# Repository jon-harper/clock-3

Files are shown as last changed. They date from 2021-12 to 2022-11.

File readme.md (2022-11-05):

# Clock 3

| First Print | Completed Panels |
|---|---|
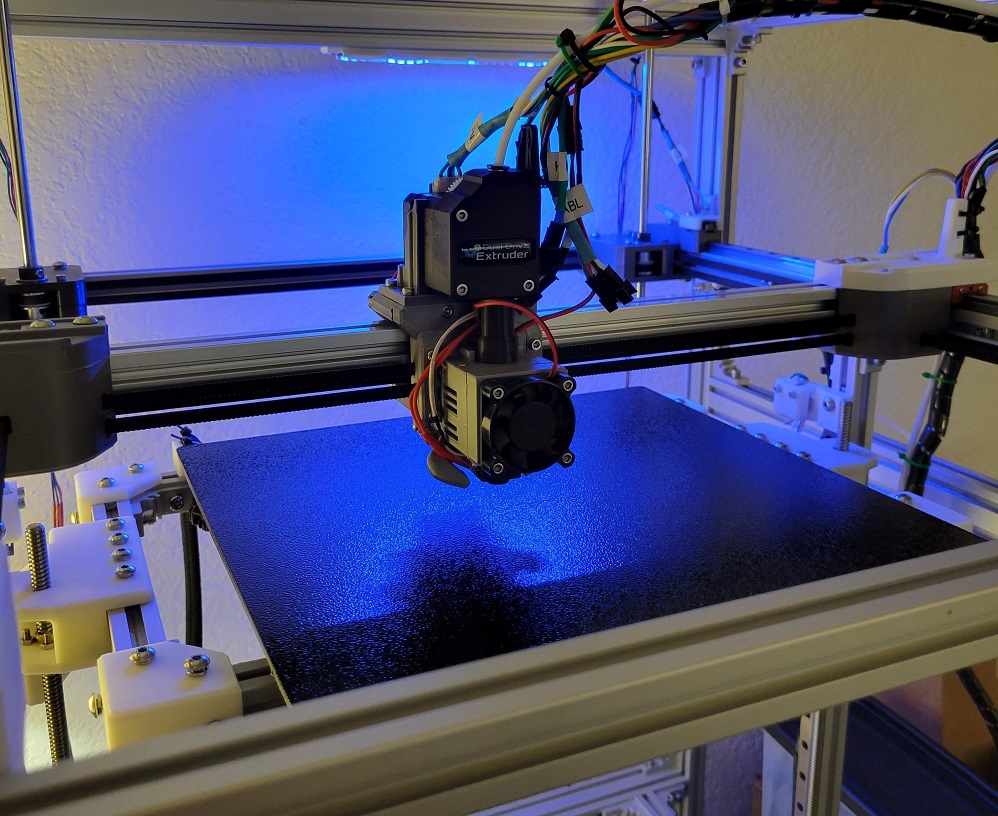
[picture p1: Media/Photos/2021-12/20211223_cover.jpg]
Cover photo of hotend
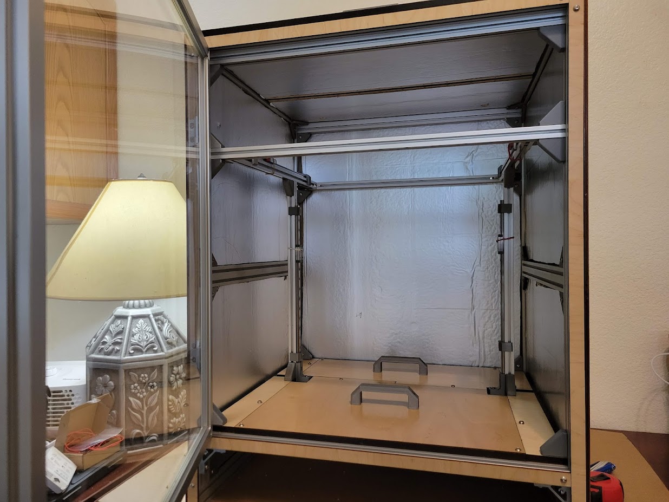
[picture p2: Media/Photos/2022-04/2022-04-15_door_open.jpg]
Cover photo with door open
|  |  |

This is the evolution of the concept of a fully enclosed, temperature-controlled 3D printer with externally mounted steppers motors. The idea of building an enclosed 3D printer to suit my specific needs came during the 2021 Winter Storm. Clock 1 was a thought experiment to enclose an Ender 5-like Cartesian printer. Clock 2 was a from-scratch CoreXY printer that I largely built before acquiring the ability to safely print ABS.

Clock 3 is a complete redesign incorporating most of the common, off-the-shelf components from Clock 2. It incorporates lessons from repeated assembly/disassembly of Clock 2, successful concepts from other projects, and a lot of experimentation with ABS in an enclosure. Clock 3 is a working name for this project and is not final.

## Status

The core Fusion 360 files are pretty trashed due to interdependancies. I've had to halt development for now.

~~Documentation of the initial prootype is ongoing and active. The most recent compiled markdown can be viewed at [jon-harper.github.io/clock-3/](https://jon-harper.github.io/clock-3/). Follow-on releases will address minor issues discovered in the process that do not require immediate resolution.~~

## Notes

- Klipper firmware for Clock 3 is available [here](../clock3-klipper).
- The Clock Face project is [here](../clock-face), which revises the physical display and menu system for Klipper.
- The Fusion 360 model is not published yet, but you can find the project's Python scripts [here](../Clock3Scripts)
- This project is very much under active development, [**first printing on 12/21/2021**](/Media/Cropped/20211221_Hotend.jpg).
- Head to the [Media](/Media) folder for renders and photos of the prototype.

# Organization

## Naming Scheme

### STL Files

STLs are numbered sequentially to help with assembly. The number of each component is printed discreetly on each piece so that it is either concealed or very hard to see after installation. Each *component* falls into one of several *categories* and is identified by either its name or location. Components that come in left and right versions have *chirality*.

The printed text on each component also include an L or R for chiral components to help with identification. Some miscellanious and very basic parts lack numbers due to size or geometry constraints.

Example: `01 - XY - Pulleys - L Bottom.stl`

You can find all of the printable files in the [STL](STL/) folder along with a list of [part codes](Docs/Part%20Codes.md).

### Component Labeling

What one board labels as "THB" another may label as "TB". Likewise, endstop/limit switch connector abbreviations (and pin order!) are not standard, inasmuch as anything in 3D printing is standardized. To that end, a single nomenclature is adopted for part labels. Each connector has a two- or three-letter code for labeling panels and wiring. Your actual wiring may use a different system, but printed parts with labels follow this pattern. It is recommended for continuity with printed parts and documentation to use the same. The full part list may be found in the [`Docs`](Docs/) folder.

## Misc.

There are a number of tools to help determine parametric details such as the ideal M5 screw hole size or the proper hole size for your brand of brass inserts. These can be found in the `STL/Tools` folder and are meant to be printed. The results can be fed back in to the Fusion model and then exported for printing. Stock exported STL files will come with default tolerances and may not fit as precisely.

There is also a `CAD/Tools` folder with parametric tools such as an LED channel.

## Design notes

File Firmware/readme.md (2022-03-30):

# Firmware for Clock 3

Clock 3 runs on Klipper. Marlin and/or RepRapFirmware *might* be able to run the printer, but a lot of features would be missing, such as the camera.

## Klipper Config Files

You can find the `.cfg` files in the [clock3-klipper](../../../../clock3-klipper) repository. It's a separate repository so that it can be cloned directly into a subdirectory of your `~/klipper_config` directory.

## Macros?

As I build up a collection of Klipper macros, I will create an additional repository for general Klipper macros. Any Clock 3-specific macros will likely be part of the [clock3-klipper](../../../../clock3-klipper) repository.

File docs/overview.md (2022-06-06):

---
title: Overview
summary: General overview page for the documentation.
authors: Jon Harper
date: 2022-04-09
---

This site acts as a central documentation point for the Clock 3 project.

## About

For an overview, see the About section pages:

- A list of [features](about/features.md)
- A [gallery](about/gallery.md) of renders and prototype photos
- [Development goals](about/goals.md) for this project
- [Frequently Asked Questions](about/faq.md)

## Status

The Status section contains more details:

- A regularly updated [changelog](status/changelog.md)
- The current and past [releases](status/releases.md)
- The release [roadmap](status/roadmap.md)

## Documentation

In addition, there are help and guides for:

- Sourcing materials
- Fabricating parts
- Assembly (*in progress*)
- Initial configuration (*pending*)

This is a large project with one developer, so this documentation will evolve iteratively and gradually. Feedback is welcome via the [GitHub repository](https://github.com/jon-harper/clock3-docs).

### Bill of Materials

This documentation includes a general [Sales Bill of Materials](/bom/) to guide purchasing and decision making. This is a list of what you will need to actually purchase or have on hand. Some of the materials will need to be modified, fabricated, or permanently used to make other parts before or during assembly. The list of all parts once the raw materials are consumed and ready for assembly is the [Assembly Bill of Materials]().

Think of the Sales BOM as what you need to buy; the Assembly BOM is what you'll use to build.

The Clock 3 repository contains a [more detailed version of these files](https://github.com/jon-harper/clock-3/tree/main/BOM).

### Assembly

We've assembled and then broken down the Clock 3 prototype repeatedly so that you don't have to do the same with yours. Assembly of Clock 3 is meant to be logical, intuitive, and easy: every wire is pre-measured, every heated insert accounted for.

It's a time investment to get everything ready, but the result is a very straightforward assembly process.

### Configuration

Clock 3 runs on [MainsailOS](https://github.com/mainsail-crew/MainsailOS), which is an all-in-one OS for running [Klipper](https://www.klipper3d.org/) firmware with a clean web frontend.

Clock 3 relies on a modified Klipper 12864 menu system and display with more functionality than the stock menu system. 

We've setup several repositories so that you can simply `git clone` the configuration files directly onto your Raspberry Pi in the appropriate directories.

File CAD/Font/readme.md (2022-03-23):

# Hack, a Font Face

This project uses [Hack](https://sourcefoundry.org/hack/#download) as a general-purpose, easily printable, monospace font. You'll need to download it to open the source model in Fusion 360.

There's a [download page](https://sourcefoundry.org/hack/#download) or you can grab them from this Git source folder.

It's also a great font face for coding or scripting if you need a new one.

Hack is released under the [MIT license](https://github.com/source-foundry/Hack/blob/master/LICENSE.md). A copy is in this folder, as well.

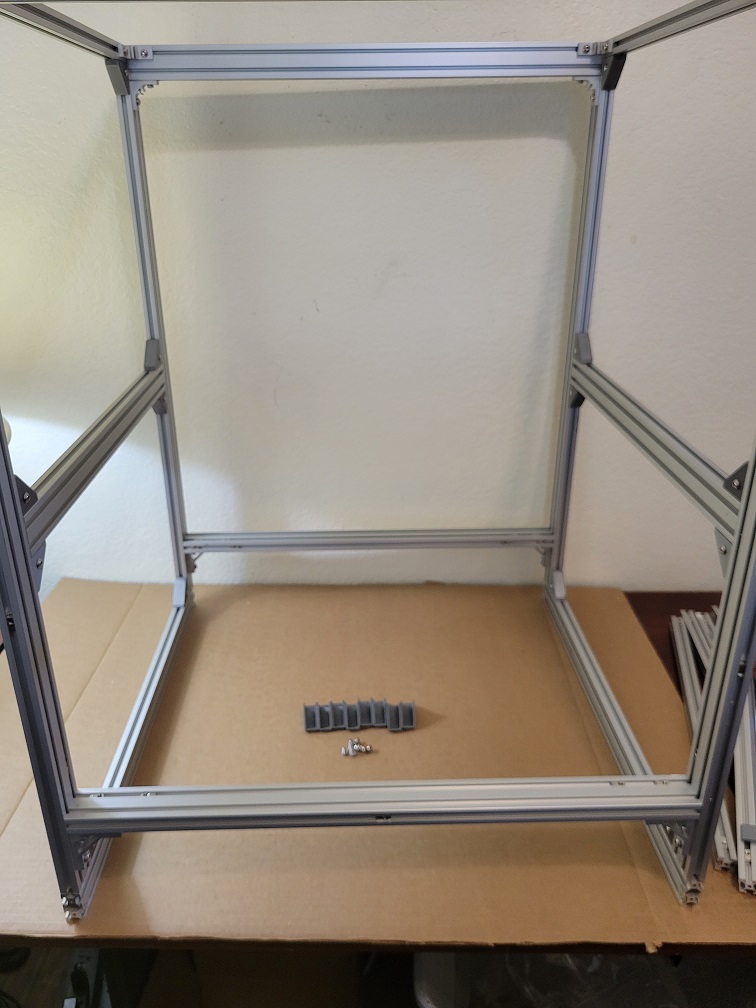
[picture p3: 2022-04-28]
docs/img/bracket_covers_center/brackets_overview.jpg

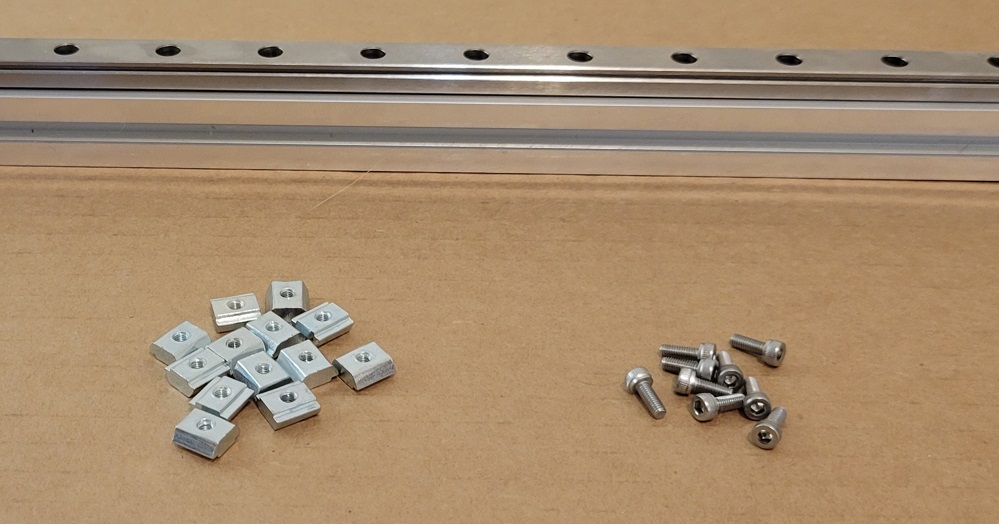
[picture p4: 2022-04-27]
docs/img/rail_install/overview.jpg

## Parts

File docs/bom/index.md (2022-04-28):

---
title: Bill of Materials Introduction
summary: An introduction to reading the Clock 3 Bill of Materials.
authors: Jon Harper
date: 2022-04-05
---

*This document is actively being refined and edited for mistaeks.*
## Overview

We designed Clock 3 with several rules related to sourcing and parts in mind:

- Every new line added to the BOM has an up front cost.
- Rare parts are expensive and hard to find, by definition.
- Standardized and *de facto* standard parts are cheaper and have more suppliers.
- Custom fabricated anything is expensive.

With those rules in mind, we aim to both keep costs down and make sourcing parts as simple as possible.

## Keeping Track

Every component that goes in to making a Clock 3 printer is assigned an ID number and categorized in several ways.
 
- Is it a printed part or something purchased?
- Does it require modification or assembly, such as finished cables or insulation cut to size?
- Is it an aid for assembly or maintence that isn't part of the printer itself?
- Finally, what is the general function of the part in the printer (e.g. frame, electronics, motion)?

## Categorization

Let's talk about identifying the things you'll need to print, buy, or make. Parts are given a number with a two letter prefix and a three-digit number code, for example `PN001`.

### Prefixes

`MN`: Parts in the format `MN###` are raw materials. During the assembly process, they'll be modified or used to make something else. Typically this can't be reversed: examples are connector pins and heat shrink tubing. This list is not exhaustive--if you won't need to buy or assemble it, it's not given a number. For example, you probably won't cut the frame extrusions yourself, so we don't include the raw aluminum in the list.

`UN`: These parts aren't actually part of the printer but you will need them to put it together or keep it running. You may already have some or all of these on hand, like a soldering iron or set of Metric hex wrenches.

`PN`: These are finished parts, whether printed, purchased, or made from materials. They come in the format `PN###`.

!!! note
    If the number after `PN` is less than 399, it's a printed part.

### Fabricated parts

There are several kinds of these:

- Printed parts, with or without heat set inserts
- Cables and wiring harnesses
- Cut extrusions and panels

With the exception of cables, all of these have part numbers in the form `PN`. Cables also have an ID, but it is tracked based on the component that the cable powers. There's more on that later in the assembly guide.

All of these fabricated parts require materials (parts starting with `MN`). Consequently, some parts in the BOM are made entirely from materials.

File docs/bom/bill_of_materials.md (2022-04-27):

# Bill of Materials

The columns of this list are abbreviated for readability and reference. The
[Excel spreadsheet](https://github.com/jon-harper/clock-3/blob/main/BOM/bill_of_materials.xlsx)
version contains additional columns that are helpful in sourcing.

!!! warning
    The script that auto-generates this list does not read decimal values. Anything measured in length
    is measured in centimeters (cm) instead of meters (m) to work around this.
    
!!! note
    - Materials are used in fabricating parts found later in the Bill of Materials or cable
      list. Some parts, particularly the acrylic and wood panels, will likely require outside
      fabrication.
    - All reference URLs and suppliers are purely for assistance in sourcing materials and are
      not endorsed.
    - The "Supplies" category includes a large number of components that are often already in the
      hands of experienced makers. As such, the list is primarily for reference and is not formally
      part of the Bill of Materials.

## Materials

| ID | Description | UOM | Qty | Notes |
|:---|:---|----:|----:|:---|
| MN001 | [Activated Carbon, Virgin Coconut, 4-8mm](https://www.amazon.com/gp/product/B00XIIH43W) | 1 | lb | 0.5lb to start; have heard negative things about this supplier recently |
| MN002 | [Thermal Glue](https://www.amazon.com/gp/product/B07TSH6MNT) | 1 | ea |  |
| MN004 | [Zip ties, 4"](https://www.amazon.com/AmazonBasics-Multi-Purpose-Cable-Ties-200-Piece/dp/B087MKMSDY) | 1 | pk | Qty varies based on cofiguration and personal preference |
| MN100 | [Polyisocyanurate Foam, 1/2", 4'x8' sheet](https://www.homedepot.com/p/RMAX-Pro-Select-R-Matte-Plus-3-1-2-in-x-4-ft-x-8-ft-R-3-2-Foam-Insulation-Board-637902/313501506) | 1 | ea | Can substitute 3/4" and 1" in places for better insulation |
| MN101 | Plywood sheet, 12mm thickness, 4'x5' | 2 | ea | For paneling |
| MN102 | Acrylic sheet, 3mm thickness, 4'x5' | 1 | ea | For door windows |
| MN103 | Plywood sheet, 6mm thickness, 4'x5' | 1 | ea | For front panels |
| MN104 | [Wire loom, PET, 1/4"](https://www.amazon.com/gp/product/B08D3RXL7T) | 260 | cm | Minimum quantity. More cables can be wrapped. |
| MN105 | [Wire loom, PET, 1/2"](https://www.amazon.com/gp/product/B08D3RXL7T) | 120 | cm |  |
| MN107 | [Heat shrink tubing, various sizes](https://www.amazon.com/gp/product/B07WWWPR2X) | 1 | pk | 2.5mm - 4mm, mostly |
| MN108 | [Heat shrink tubing, 13mm](https://www.amazon.com/XHF-Inch-13mm-Waterproof-Insulation/dp/B07FPDBGYH) | 45 | cm | For PET loom ends |
| MN110 | [Hookup Wire, Silicone, 16 AWG](https://www.amazon.com/Electrical-Gauge-Silicone-Cable-Black/dp/B0746HRVZP) | 625 | cm | Red, black and optionally green or yellow |
| MN111 | [Hookup Wire, Silicone, 20 AWG](https://www.amazon.com/gp/product/B07T4SYVYG) | 520 | cm | Red, black |
| MN112 | [Hookup Wire, Silicone, 24 AWG](https://www.amazon.com/gp/product/B087TJNJZS/) | 8820 | cm | OR 26 awg |
| MN113 | [Hookup Wire, Silicone, 12 AWG](https://www.amazon.com/BNTECHGO-Silicone-Flexible-Strands-Stranded/dp/B01AQU3ST8) | 60 | cm | OR 13 awg; red and black |
| MN201 | [JST SM Pin Socket](https://www.digikey.com/en/products/detail/jst-sales-america-inc/SYF-001T-P0-6-LF-SN/2027280) | 88 | ea |  |
| MN202 | [JST SM Connector, 2.54mm, Male, 2 Pin](https://www.digikey.com/en/products/detail/jst-sales-america-inc/SMR-02V-B/764265) | 12 | ea |  |
| MN203 | [JST SM Connector, 2.54mm, Male, 3 Pin](https://www.digikey.com/en/products/detail/jst-sales-america-inc/SMR-03V-B/5702345) | 10 | ea |  |
| MN204 | [JST SM Connector, 2.54mm, Male, 4 Pin](https://www.digikey.com/en/products/detail/jst-sales-america-inc/SMR-04V-B/2137107) | 6 | ea |  |
| MN205 | [JST SM Connector, 2.54mm, Male, 5 Pin](https://www.digikey.com/en/products/detail/jst-sales-america-inc/smr-05v-b/3622430) | 2 | ea |  |
| MN210 | [JST SM Connector, 2.54mm, Female, 2 Pin](https://www.digikey.com/en/products/detail/jst-sales-america-inc/SMP-02V-BC/1835574) | 12 | ea |  |
| MN211 | [JST SM Connector, 2.54mm, Female, 3 Pin](https://www.digikey.com/en/products/detail/jst-sales-america-inc/SMP-03V-BC/2514249) | 10 | ea |  |
| MN212 | [JST SM Connector, 2.54mm, Female, 4 Pin](https://www.digikey.com/en/products/detail/jst-sales-america-inc/SMP-04V-BC/7230521) | 6 | ea |  |
| MN213 | [JST SM Connector, 2.54mm, Female, 5 Pin](https://us.misumi-ec.com/vona2/detail/222000498388/?HissuCode=SMP-05V-BC) | 2 | ea | Digikey doesn't carry this, for some reason |
| MN220 | [JST XH Pin Socket](https://www.digikey.com/en/products/detail/jst-sales-america-inc/SXH-002T-P0-6/1651063) | 55 | ea |  |
| MN221 | [JST XH Connector, 2.5mm, Female, 2 Pin](https://www.digikey.com/en/products/detail/jst-sales-america-inc/XHP-2/555485) | 6 | ea |  |
| MN222 | [JST XH Connector, 2.5mm, Female, 3 Pin](https://www.digikey.com/en/products/detail/jst-sales-america-inc/XHP-3/1651017) | 9 | ea |  |
| MN223 | [JST XH Connector, 2.5mm, Female, 4 Pin](https://www.digikey.com/en/products/detail/jst-sales-america-inc/XHP-4/683353) | 3 | ea |  |
| MN240 | [JST PH Connector, 2.0mm, Female, 6 Pin](https://www.digikey.com/en/products/detail/adafruit-industries-llc/4422/11497499) | 3 | ea | Only needed if steppers have integrated connectors |
| MN241 | [JST PH Pin Socket](https://www.digikey.com/en/products/detail/adafruit-industries-llc/4422/11497499) | 12 | ea | Only needed if steppers have integrated connectors |
| MN242 | [XT 60 Connector Set, 12 awg 150mm pigtails](https://www.amazon.com/gp/product/B073QJWVVK/) | 1 | pk | Optional |
| MN250 | Ring Connector, 18-24 awg | 3 | ea | Number varies based on configuration |
| MN251 | Ring Connector, 14-18 awg | 9 | ea | Number varies based on configuration |
| MN252 | Spade Connector, 14-18 awg | 5 | ea |  |
| MN253 | Butt Splice, 12-14 awg | 4 | ea | Without XT60, only two needed. |
| MN260 | [Micro Fit 3 Connector Pin](https://www.digikey.com/en/products/detail/molex/0430310009/252485) | 4 | ea |  |
| MN261 | [Micro Fit 3 Connector Socket](https://www.digikey.com/en/products/detail/molex/0430300009/252481) | 4 | ea |  |
| MN262 | [Micro Fit 3 Connector, 2 pin, 2 Row, Male](https://www.digikey.com/en/products/detail/molex/0430250200/252496) | 2 | ea |  |
| MN263 | [Micro Fit 3 Connector, 2 pin, 2 Row, Panel Mount](https://www.digikey.com/en/products/detail/molex/0430200200/252490) | 2 | ea |  |

## Printed

| ID | Description | UOM | Qty | Notes |
|:---|:---|----:|----:|:---|
| PN001 | [XY Pulleys, L Bottom](001 - XY Pulleys, L Bottom.stl) | 1 | ea |  |
| PN002 | [XY Pulleys, L Top](002 - XY Pulleys, L Top.stl) | 1 | ea |  |
| PN003 | [XY Pulleys, R Bottom](003 - XY Pulleys, R Bottom.stl) | 1 | ea |  |
| PN004 | [XY Pulleys, R Top](004 - XY Pulleys, R Top.stl) | 1 | ea |  |
| PN005 | [XY Joint, L Top](005 - XY Joint, L Top.stl) | 1 | ea |  |
| PN006 | [XY Joint, L Mid](006 - XY Joint, L Mid.stl) | 1 | ea |  |
| PN007 | [XY Joint, L Bottom](007 - XY Joint, L Bottom.stl) | 1 | ea |  |
| PN008 | [XY Joint, R Top](008 - XY Joint, R Top.stl) | 1 | ea |  |
| PN009 | [XY Joint, R Mid](009 - XY Joint, R Mid.stl) | 1 | ea |  |
| PN010 | [XY Joint, R Bottom](010 - XY Joint, R Bottom.stl) | 1 | ea |  |
| PN011 | [XY Tensioner, Bolt Receiver](011 - XY Tensioner, Bolt Receiver.stl) | 2 | ea |  |
| PN012 | [XY Tensioner, Idler Seat](012 - XY Tensioner, Idler Seat.stl) | 2 | ea |  |
| PN013 | [XY Tensioner, Tensioner Cap](013 - XY Tensioner, Tensioner Cap.stl) | 2 | ea |  |
| PN014 | [XY Tensioner, Guide Frame](014 - XY Tensioner, Guide Frame.stl) | 2 | ea |  |
| PN015 | [XY Steppers, Vibration Damper, TPU](015 - XY Steppers, Vibration Damper, TPU.stl) | 2 | ea | No ID tag |
| PN016 | [XY Steppers, Stepper Mount](016 - XY Steppers, Stepper Mount.stl) | 2 | ea |  |
| PN017 | [XY Motion, L Y Rail Guide](017 - XY Motion, L Y Rail Guide.stl) | 1 | ea |  |
| PN018 | [XY Motion, R Y Rail Guide](018 - XY Motion, R Y Rail Guide.stl) | 1 | ea | Also acts as limit switch mount |
| PN019 | [Z Motion, Lower Rail Bracket](019 - Z Motion, Lower Rail Bracket.stl) | 2 | ea |  |
| PN020 | [Z Axis, Bed Corner Bracket](020 - Z Axis, Bed Corner Bracket.stl) | 4 | ea |  |
| PN021 | [Z Axis, L Gantry](021 - Z Axis, L Gantry.stl) | 1 | ea |  |
| PN022 | [Z Axis, R Gantry](022 - Z Axis, R Gantry.stl) | 1 | ea |  |
| PN023 | [Z Axis, L Stepper Mount](023 - Z Axis, L Stepper Mount.stl) | 1 | ea |  |
| PN024 | [Z Axis, R Stepper Mount](024 - Z Axis, R Stepper Mount.stl) | 1 | ea |  |
| PN025 | [Z Motion, L Limit Switch Mount](025 - Z Motion, L Limit Switch Mount.stl) | 1 | ea |  |
| PN026 | [Z Motion, R Limit Switch Mount](026 - Z Motion, R Limit Switch Mount.stl) | 1 | ea |  |
| PN027 | [Z Axis, L Lead Screw Plate](027 - Z Axis, L Lead Screw Plate.stl) | 1 | ea |  |
| PN028 | [Z Axis, R Lead Screw Plate](028 - Z Axis, R Lead Screw Plate.stl) | 1 | ea |  |
| PN029 | [Z Axis, Bed Wire Support](029 - Z Axis, Bed Wire Support.stl) | 1 | ea |  |
| PN030 | [X Gantry, Carriage Mount](030 - X Gantry, Carriage Mount.stl) | 1 | ea |  |
| PN031 | [X Gantry, Top Mount](031 - X Gantry, Top Mount.stl) | 1 | ea |  |
| PN032 | [X Gantry, Back Mount](032 - X Gantry, Back Mount.stl) | 1 | ea |  |
| PN033 | [X Gantry, Front Mount](033 - X Gantry, Front Mount.stl) | 1 | ea |  |
| PN034 | [X Gantry, L Belt Clamp](034 - X Gantry, L Belt Clamp.stl) | 1 | ea | No ID tag |
| PN035 | [X Gantry, R Belt Clamp](035 - X Gantry, R Belt Clamp.stl) | 1 | ea | No ID tag |
| PN040 | [Toolhead, Hotend Mounting Bracket](040 - Toolhead, Hotend Mounting Bracket.stl) | 1 | ea | No ID tag |
| PN041 | [Toolhead, Hotend Locking Collar](041 - Toolhead, Hotend Locking Collar.stl) | 1 | ea | No ID tag |
| PN042 | [Toolhead, Cooling Fan Intake](042 - Toolhead, Cooling Fan Intake.stl) | 1 | ea | No ID tag |
| PN043 | [Toolhead, PTFE Collar, TPU](043 - Toolhead, PTFE Collar, TPU.stl) | 1 | ea | No ID tag |
| PN044 | [Toolhead, EVA Fan Duct](044 - Toolhead, EVA Fan Duct.stl) | 1 | ea | No ID tag |
| PN045 | [Toolhead, Part Fan Mount](045 - Toolhead, Part Fan Mount.stl) | 1 | ea | No ID tag |
| PN051 | [Toolhead, BLTouch Mount](051 - Toolhead, BLTouch Mount.stl) | 1 | ea | No ID tag |
| PN061 | [Toolhead, BMG Mount](061 - Toolhead, BMG Mount.stl) | 1 | ea |  |
| PN070 | [Electrical, R Panel](070 - Electrical, R Panel.stl) | 1 | ea | JST-SM connector panel |
| PN071 | [Electrical, L Panel](071 - Electrical, L Panel.stl) | 1 | ea | JST-SM connector panel |
| PN072 | [Electrical, R Panel Back Plate](072 - Electrical, R Panel Back Plate.stl) | 1 | ea |  |
| PN073 | [Electrical, L Panel Back Plate](073 - Electrical, L Panel Back Plate.stl) | 1 | ea |  |
| PN076 | [Electrical, L Octopus Board Mount](076 - Electrical, L Octopus Board Mount.stl) | 1 | ea |  |
| PN077 | [Electrical, R Octopus Board Mount](077 - Electrical, R Octopus Board Mount.stl) | 1 | ea |  |
| PN082 | [Lighting, LED Guide, 12mm](082 - Lighting, LED Guide, 12mm.stl) | 3 | ea | 60 LEDs/m |
| PN083 | [Electrical, L RPi Board Mount](083 - Electrical, L RPi Board Mount.stl) | 1 | ea |  |
| PN084 | [Electrical, R RPi Board Mount](084 - Electrical, R RPi Board Mount.stl) | 1 | ea |  |
| PN086 | [Electrical, PSU Mount](086 - Electrical, PSU Mount.stl) | 2 | ea |  |
| PN087 | [Electrical, Camera Mount](087 - Electrical, Camera Mount.stl) | 1 | ea | No ID tag |
| PN088 | [Electrical, Camera Stand](088 - Electrical, Camera Stand.stl) | 1 | ea |  |
| PN090 | [Misc, Corner Bracket Cover](090 - Misc, Corner Bracket Cover.stl) | 46 | ea | Count not final |
| PN091 | [Misc, Limit Switch Cap](091 - Misc, Limit Switch Cap.stl) | 4 | ea | No ID tag |
| PN092 | [Misc, Printer Base Foot, TPU](092 - Misc, Printer Base Foot, TPU.stl) | 4 | ea | No ID tag |
| PN093 | [XY Motion, X Limit Switch Mount](093 - XY Motion, X Limit Switch Mount.stl) | 1 | ea |  |
| PN094 | [Misc, X Gantry Service Bar](094 - Misc, X Gantry Service Bar.stl) | 2 | ea | No ID tag |
| PN095 | [Frame, Bearing Alignment Slider, TPU](095 - Frame, Bearing Alignment Slider, TPU.stl) | 4 | ea |  |
| PN096 | [Misc, T Slot Wire Anchor](096 - Misc, T Slot Wire Anchor.stl) | 17 | ea |  |
| PN099 | [XY Motion, Y Axis Front Rail Guide](099 - XY Motion, Y Axis Front Rail Guide.stl) | 2 | ea |  |
| PN100 | [Misc, Rear PTFE Tube Guide](100 - Misc, Rear PTFE Tube Guide.stl) | 1 | ea |  |
| PN102 | [Skirt, 80mm Fan Mount](102 - Skirt, 80mm Fan Mount.stl) | 3 | ea |  |
| PN103 | [Skirt, 80mm Fan Exterior Grill](103 - Skirt, 80mm Fan Exterior Grill.stl) | 3 | ea |  |
| PN104 | [Skirt, L Front End](104 - Skirt, L Front End.stl) | 1 | ea | HDMI, USB, Ethernet plugs |
| PN105 | [Skirt, R Front End](105 - Skirt, R Front End.stl) | 1 | ea | Power switch |
| PN106 | [Skirt, L Rear End](106 - Skirt, L Rear End.stl) | 1 | ea | A stepper plug |
| PN107 | [Skirt, R Rear End](107 - Skirt, R Rear End.stl) | 1 | ea | IEC (power), B stepper plugs |
| PN108 | [Skirt, Hexagon Grill](108 - Skirt, Hexagon Grill.stl) | 4 | ea |  |
| PN110 | [Skirt, SD Card Reader Mount](110 - Skirt, SD Card Reader Mount.stl) | 1 | ea |  |
| PN111 | [Skirt, 80mm Fan Finger Guard](111 - Skirt, 80mm Fan Finger Guard.stl) | 3 | ea |  |
| PN112 | [Skirt, Display Mount](112 - Skirt, Display Mount.stl) | 1 | ea |  |
| PN113 | [Skirt, Display Slot](113 - Skirt, Display Slot.stl) | 1 | ea |  |
| PN120 | [Frame, PTFE Coupler](120 - Frame, PTFE Coupler.stl) | 1 | ea |  |
| PN121 | [Frame, Exhaust Coupler](121 - Frame, Exhaust Coupler.stl) | 1 | ea |  |
| PN122 | [Frame, PTFE Coupling Guide, TPU](122 - Frame, PTFE Coupling Guide, TPU.stl) | 1 | ea |  |
| PN123 | [Z Axis, L Z Slider Mount](123 - Z Axis, L Z Slider Mount.stl) | 1 | ea |  |
| PN124 | [Z Axis, R Z Slider Mount](124 - Z Axis, R Z Slider Mount.stl) | 1 | ea |  |
| PN125 | [Frame, Pull Handle](125 - Frame, Pull Handle.stl) | 3 | ea |  |
| PN126 | [Frame, Pull Handle, T Slot](126 - Frame, Pull Handle, T Slot.stl) | 1 | ea | V Slot Door Handle |
| PN127 | [Frame, Wire Conduit, Top, TPU](127 - Frame, Wire Conduit, Top, TPU.stl) | 2 | ea |  |
| PN128 | [Frame, Wire Conduit, Bottom, TPU](128 - Frame, Wire Conduit, Bottom, TPU.stl) | 2 | ea |  |
| PN200 | [Filtration, Exhaust Adapter, TPU](200 - Filtration, Exhaust Adapter, TPU.stl) | 1 | ea | TPU/PETG |
| PN201 | [Filtration, Fan Intake Gasket, TPU](201 - Filtration, Fan Intake Gasket, TPU.stl) | 2 | ea | TPU/PETG |
| PN202 | [Filtration, Fan Intake Duct](202 - Filtration, Fan Intake Duct.stl) | 1 | ea | PETG/ABS |
| PN203 | [Filtration, HEPA Filter Sleeve](203 - Filtration, HEPA Filter Sleeve.stl) | 1 | ea | PETG/ABS |
| PN204 | [Filtration, HEPA Intake Duct](204 - Filtration, HEPA Intake Duct.stl) | 1 | ea | PETG/ABS |
| PN205 | [Filtration, HEPA Latch, TPU](205 - Filtration, HEPA Latch, TPU.stl) | 2 | ea | TPU/PETG |
| PN206 | [Filtration, AC Tank Gasket, TPU](206 - Filtration, AC Tank Gasket, TPU.stl) | 1 | ea | TPU/PETG |
| PN207 | [Filtration, Base Stand](207 - Filtration, Base Stand.stl) | 1 | ea | PETG/ABS |
| PN210 | [Filtration, AC Tank Lid](210 - Filtration, AC Tank Lid.stl) | 1 | ea | PETG/ABS |
| PN211 | [Filtration, AC Tank Filter Ring](211 - Filtration, AC Tank Filter Ring.stl) | 2 | ea | PETG/ABS |
| PN212 | [Filtration, AC Tank, 50mm](212 - Filtration, AC Tank, 50mm.stl) | 1 | ea | PETG/ABS |

## Toolhead

| ID | Description | UOM | Qty | Notes |
|:---|:---|----:|----:|:---|
| PN400 | [E3D V6 Hotend (Direct Drive)](https://www.amazon.com/Genuine-E3D-All-Metal-Universal-V6-175-MO/dp/B074DHD751) | 1 | ea | Or compatible clone; GCR uses incompatible thermistor |
| PN450 | [Bondtech BMG Extruder](https://www.amazon.com/Genuine-Bondtech-BMG-Extruder-EXT-BMG/dp/B07DGL43SQ) | 1 | ea | Or compatible clone |
| PN485 | [BLTouch V3.1](https://www.amazon.com/ANTCLABS-BLTouch-Leveling-Premium-Extension/dp/B076PQG1FF) | 1 | ea | Or compatible clone |

## Fastener

| ID | Description | UOM | Qty | Notes |
|:---|:---|----:|----:|:---|
| PN500 | [Screw, M3-0.5 x 6mm SHCS](https://www.amazon.com/10-M3-0-50-6mm-Stainless-MonsterBolts/dp/B078LBVG2C) | 46 | ea |  |
| PN501 | [Screw, M3-0.5 x 8mm SHCS](https://www.amazon.com/10-M3-0-50-6mm-Stainless-MonsterBolts/dp/B078L47SCG) | 161 | ea |  |
| PN502 | [Screw, M3-0.5 x 12mm SHCS](https://www.amazon.com/10-M3-0-50-6mm-Stainless-MonsterBolts/dp/B078KZRT8L) | 23 | ea |  |
| PN503 | [Screw, M3-0.5 x 16mm SHCS](https://www.amazon.com/10-M3-0-50-6mm-Stainless-MonsterBolts/dp/B078LCYXPL) | 19 | ea |  |
| PN504 | [Screw, M3-0.5 x 20mm, SHCS](https://www.amazon.com/10-M3-0-50-6mm-Stainless-MonsterBolts/dp/B078L48BMP) | 7 | ea |  |
| PN505 | [Screw, M3-0.5 x 25mm SHCS](https://www.amazon.com/10-M3-0-50-6mm-Stainless-MonsterBolts/dp/B08BBVKXWC) | 8 | ea | Long M3 screws can usually be found in multi-size packs on Amazon (25-45mm) |
| PN506 | [Screw, M3-0.5 x 30mm SHCS](https://www.amazon.com/10-M3-0-50-6mm-Stainless-MonsterBolts/dp/B078KZXP5P) | 8 | ea | Long M3 screws can usually be found in multi-size packs on Amazon (25-45mm) |
| PN507 | [Screw, M3-0.5 x 35mm SCHS](https://www.amazon.com/gp/product/B078L42CXS/) | 19 | ea | Long M3 screws can usually be found in multi-size packs on Amazon (25-45mm) |
| PN508 | [Screw, M3-0.5 x 40mm SHCS](https://www.amazon.com/10-M3-0-50-6mm-Stainless-MonsterBolts/dp/B07JHB1G85) | 6 | ea | Long M3 screws can usually be found in multi-size packs on Amazon (25-45mm) |
| PN509 | [Screw, M3-0.5 x 45mm SHCS](https://us.misumi-ec.com/vona2/detail/221000551310/?ProductCode=CSHZ-SUS-M3-45) | 4 | ea | Long M3 screws can usually be found in multi-size packs on Amazon (25-45mm) |
| PN530 | [Screw, M5-0.8 x 8mm BHCS](https://www.amazon.com/M5-0-80-Stainless-Button-Socket-Screws/dp/B077WLXQWG) | 53 | ea |  |
| PN532 | [Screw, M5-0.8 x 12mm BHCS](https://www.amazon.com/M5-0-80-Stainless-Button-Socket-Screws/dp/B078CQLGKX) | 216 | ea | 200pc: https://www.amazon.com/M5-0-8-Button-Available-Stainless-Machine/dp/B07VRZYMP6 |
| PN533 | [Screw, M5-0.8 x 16mm BHCS](https://www.amazon.com/M5-0-80-Stainless-Button-Socket-Screws/dp/B077WLQ1LZ) | 38 | ea |  |
| PN534 | [Screw, M5-0.8 x 25mm BHCS](https://www.amazon.com/M5-0-80-Stainless-Button-Socket-Screws/dp/B077WCYJB9) | 22 | ea |  |
| PN535 | [Screw, M5-0.8 x 60mm BHCS](https://www.amazon.com/M5-0-8-Button-Available-Stainless-Machine/dp/B08FJCS884) | 4 | ea | May be hard to find in BH, SHCS also works. |
| PN536 | [Screw, M5-0.8 x 20mm BHCS](https://www.amazon.com/M5-0-80-Stainless-Button-Socket-Screws/dp/B077WKWHXC?th=1) | 4 | ea |  |
| PN537 | [Screw, M5-0.8 x 50mm BHCS](https://www.amazon.com/gp/product/B08HLW8LW6) | 6 | ea | May be hard to find in BH, SHCS also works. |
| PN550 | [Screw, M4-0.7 x 35mm FHCS](https://www.amazon.com/gp/product/B07SDFX766) | 4 | ea | Included with bed leveling nuts |
| PN551 | [Set Screw, M4-0.7 x 4mm](https://www.amazon.com/gp/product/B07PK8ZJTV) | 24 | ea | Included with hidden corner brackets |
| PN552 | [Screw, M4-0.7 x 16mm SHCS](https://www.amazon.com/gp/product/B07RMZCLZ3) | 4 | ea | Included with spider couplers |
| PN553 | [Screw, M5-0.8 x 16mm SHCS](https://www.amazon.com/20-M5-0-80-35mm-Stainless-MonsterBolts/dp/B078L3YNS3) | 8 | ea | Door corners only. MISUMI corners ships with screws. |
| PN555 | [Screw, M5-0.8 x 14mm FHCS](https://www.amazon.com/Countersunk-Socket-Screws-20-piece-Stainless/dp/B07CNTZMNV) | 8 | ea | M5-0.8 x 15mm will also work. 16mm is too long. |
| PN556 | [Set Screw, M4-0.7 x 4mm](https://www.amazon.com/Befenybay-Collar-Shaft-Screw-Printer/dp/B07V41FRZS) | 4 | ea | Included with 8mm Lock Collars |
| PN557 | [Screw, M4-0.7 x 8mm BHCS](https://www.amazon.com/10-M4-0-70-12mm-Stainless-MonsterBolts/dp/B078YDH3LY) | 4 | ea | For PSU only |
| PN558 | [Screw, #8 x 3/4", Truss Head, Sharp Point](https://www.homedepot.com/p/Everbilt-8-x-3-4-in-Phillips-Drive-Truss-Head-Lath-Sharp-Point-Screw-1-lb-Box-215-Pack-116102/205142852) | 24 | ea | Metric: M4 x 20mm |
| PN570 | [Hex Nut, M3](https://www.amazon.com/dp/B087R22HM2) | 14 | ea |  |
| PN571 | [Hex Nut, M4](https://www.amazon.com/dp/B087R22HM2) | 4 | ea |  |
| PN572 | [Hex Nut, M5](https://www.amazon.com/dp/B087R22HM2) | 8 | ea |  |
| PN573 | [Tee Nut, 6mm Slot, M3, Drop In](https://www.amazon.com/IEUYO-Fastener-Aluminum-Profile-Accessories/dp/B07NZKK1PM) | 23 | ea |  |
| PN574 | [Tee Nut, 6mm Slot, M5, Drop In](https://www.amazon.com/IEUYO-Fastener-Aluminum-Profile-Accessories/dp/B07NZKK1PM) | 16 | ea |  |
| PN575 | [Tee Nut, 6mm Slot, M5, Roll In](https://www.amazon.com/100-Pack-Aluminum-Extrusions-Profile-Accessories/dp/B07VHNGBWJ) | 277 | ea |  |
| PN576 | [Tee Nut, 6mm Slot, M3, Slide In](https://www.amazon.com/Boeray-Sliding-Aluminum-Extrusion-Profile/dp/B01GCDG2QE) | 80 | ea |  |
| PN577 | [Washer, M5, Split Lock](https://www.amazon.com/gp/product/B07Z2FFPCJ) | 230 | ea |  |
| PN578 | [Washer, M5x10mm](https://www.amazon.com/Steel-Washer-Plated-Finish-Metric/dp/B009OK4TZO) | 29 | ea |  |
| PN579 | [Thumb Nut, M3](https://www.amazon.com/PZRT-Nickel-Plated-Knurled-Eco-Friendly-Printers/dp/B07P627SJN) | 2 | ea | 7mm thickness is preferable |
| PN580 | [Coupler, 5mm to 8mm, Rigid](https://www.amazon.com/uxcell-Coupling-L25xD14-Coupler-Connector/dp/B07P6X8RWL) | 2 | ea | A/B steppers |
| PN581 | [Coupler, 5mm to 8mm, Spider](https://www.amazon.com/gp/product/B07RMZCLZ3) | 2 | ea | Z steppers |
| PN582 | [Lock Collar, 8mm](https://www.amazon.com/Befenybay-Collar-Shaft-Screw-Printer/dp/B07V41FRZS) | 4 | ea |  |
| PN595 | [Heat Set Insert, M3x5.7mm](https://www.amazon.com/iplusmile-Embedment-Threaded-Printing-Projects/dp/B087NBYF65) | 135 | ea |  |

## Transmission

| ID | Description | UOM | Qty | Notes |
|:---|:---|----:|----:|:---|
| PN600 | [Bearing, F688ZZ](https://www.amazon.com/uxcell-Bearing-8x16x5mm-Shielded-Bearings/dp/B07Z3F68H4) | 8 | ea |  |
| PN601 | [Bearing, F695-2RS](https://www.amazon.com/uxcell-F695-2RS-Bearing-5x13x4mm-Bearings/dp/B085D91TW1) | 20 | ea |  |
| PN610 | [Idler Pulley, 2GT-2 20T, 5mm Bore](https://www.amazon.com/gp/product/B07BPGYX3G) | 2 | ea |  |
| PN611 | [Pulley, 2GT-2, 30T, 8mm Bore](https://www.amazon.com/gp/product/B07K69SMV2) | 2 | ea |  |
| PN612 | [Belt, 2GT-2, 6mm, Fiberglass Core](https://www.amazon.com/Timing-Printer-FYSETC-Fiberglass-Reinforced/dp/B07BRKZGMS) | 400 | cm |  |
| PN620 | [Dowel Pin, 5mm OD, 25mm](https://www.amazon.com/gp/product/B07MHGHH84) | 10 | ea |  |
| PN621 | [Linear Rod, 8mm OD, 250mm](https://www.amazon.com/gp/product/B07JL1WK8B) | 2 | ea |  |
| PN631 | [Linear Rail, MGN12, 400mm](https://www.amazon.com/gp/product/B08G1M4SX8) | 5 | ea |  |
| PN632 | [Linear Rail Carriage, MGN12H](https://www.amazon.com/gp/product/B08G1M4SX8) | 5 | ea |  |
| PN642 | [Lead Screw, Tr8x4, 500mm](https://www.amazon.com/gp/product/B085FYDWYG) | 2 | ea |  |
| PN643 | [Lead Screw Nut, Tr8x4, Anti-Backlash](https://www.amazon.com/gp/product/B08DJ76YXG) | 2 | ea |  |

## Framing

| ID | Description | UOM | Qty | Notes |
|:---|:---|----:|----:|:---|
| PN700 | [Corner Bracket, Tapped](https://us.misumi-ec.com/vona2/detail/110302060920/?ProductCode=HBKTS5-C) | 56 | ea |  |
| PN701 | [Corner Bracket, Inside Hidden](https://www.amazon.com/dp/B07PK8ZJTV) | 12 | ea |  |
| PN702 | [Corner Bracket, Super Thick, Tapped](https://us.misumi-ec.com/vona2/detail/110302060830/?ProductCode=HBKUS5-C) | 4 | ea |  |
| PN710 | [Corner Bracket, Door Frame](https://us.misumi-ec.com/vona2/detail/110302375310/?ProductCode=HBLTC5) | 4 | ea |  |
| PN711 | [2020 Extrusion Hinge](https://us.misumi-ec.com/vona2/detail/110302362010/?ProductCode=HHPSN5) | 2 | ea |  |
| PN713 | [2020 Door Panel Gasket, 564mm](https://us.misumi-ec.com/vona2/detail/110302375310/?ProductCode=HFSSK5-2000) | 2 | ea | Must be cut to size |
| PN714 | [2020 Door Panel Gasket, 646mm](https://us.misumi-ec.com/vona2/detail/110302375310/?ProductCode=HFSSK5-2000) | 2 | ea | Must be cut to size |
| PN715 | [Piano Hinge, 24" x 1.25"](https://www.amazon.com/gp/product/B00GI1CWHO) | 1 | ea | 2" hole spacing |
| PN725 | [2020 Extrusion, 440mm, Milled](https://us.misumi-ec.com/vona2/detail/110302685660/?ProductCode=HFSP5-2020-440) | 1 | ea | X axis rail |
| PN726 | [2020 Extrusion, 540mm, Milled](https://us.misumi-ec.com/vona2/detail/110302685660/?ProductCode=HFSP5-2020-540) | 2 | ea | Y axis rails |
| PN727 | [2020 Extrusion, 620mm](https://us.misumi-ec.com/vona2/detail/110302683830/?ProductCode=HFS5-2020-620) | 6 | ea | Y axis crossbar, external top side bar |
| PN728 | [2020 Extrusion, 500mm](https://us.misumi-ec.com/vona2/detail/110302683830/?ProductCode=HFS5-2020-500) | 1 | ea | Z axis crossbar (X axis) |
| PN729 | [2020 Extrusion, 510mm](https://us.misumi-ec.com/vona2/detail/110302683830/?ProductCode=HFS5-2020-510) | 2 | ea | Z axis rails |
| PN730 | [2020 Extrusion, 540mm](https://us.misumi-ec.com/vona2/detail/110302683830/?ProductCode=HFS5-2020-540) | 2 | ea | Z axis crossbar (Y axis) |
| PN732 | [2020 Extrusion, 220mm](https://us.misumi-ec.com/vona2/detail/110302683830/?ProductCode=HFS5-2020-220) | 2 | ea | Bed frame |
| PN733 | [2020 Extrusion, 350mm](https://us.misumi-ec.com/vona2/detail/110302683830/?ProductCode=HFS5-2020-350) | 2 | ea | Bed frame |
| PN740 | [2040 Extrusion, 800mm](https://us.misumi-ec.com/vona2/detail/110302684350/?ProductCode=HFS5-2040-800) | 4 | ea | External vertical frame |
| PN741 | [2040 Extrusion, 620mm](https://us.misumi-ec.com/vona2/detail/110302684350/?ProductCode=HFS5-2040-620) | 4 | ea | Lower frame crossbar, all sides |
| PN742 | [2040 Extrusion, 540mm](https://us.misumi-ec.com/vona2/detail/110302684350/?ProductCode=HFS5-2040-540) | 2 | ea | Side interior crossbars |
| PN750 | [404020 Extrusion, 620mm](https://us.misumi-ec.com/vona2/detail/110302685320/?ProductCode=HFS5-404020-620) | 2 | ea | External top bar, front and rear |
| PN751 | [2020 Door Extrusion, 564mm](https://us.misumi-ec.com/vona2/detail/110302375310/?ProductCode=HFTF5-2020-564-TPW) | 2 | ea | Horizontal door frame |
| PN752 | [2020 Door Extrusion, 646mm](https://us.misumi-ec.com/vona2/detail/110302375310/?ProductCode=HFTF5-2020-646-TPW) | 2 | ea | Vertical door frame |
| PN760 | Acrylic Sheet, 577x659x3mm | 1 | ea | Inner door window |
| PN761 | Acrylic Sheet, 613x694x3mm | 1 | ea | Outer door window |
| PN769 | Wood Panel, Outside Rear | 1 | ea |  |
| PN770 | Wood Panel, Outside Right | 1 | ea |  |
| PN771 | Wood Panel, Outside Left | 1 | ea |  |
| PN772 | Wood Panel, Outside Top | 1 | ea |  |
| PN773 | Wood Panel, Top Hatch | 1 | ea |  |
| PN774 | Wood Panel, Floor Access, Rear | 1 | ea |  |
| PN775 | Wood Panel, Floor Access, Front | 1 | ea |  |
| PN776 | Wood Panel, Floor Cover, Front Left | 2 | ea |  |
| PN777 | Wood Panel, Floor Cover, Front Right | 2 | ea |  |
| PN778 | Wood Panel, Front Left | 1 | ea |  |
| PN779 | Wood Panel, Front Right | 1 | ea |  |
| PN780 | Wood Panel, Front Center | 2 | ea |  |
| PN782 | Wood Strip, Hinge Anchor | 2 | ea | 1/2" or 12mm will do. |
| PN785 | PIR Foam, 1/2", Rear Panel | 1 | ea | 3/4" will also work |
| PN786 | PIR Foam, 1/2", Left Side with Cutout | 1 | ea | 3/4" will also work |
| PN787 | PIR Foam, 1/2", Right Side with Cutout | 1 | ea | 3/4" will also work |
| PN788 | PIR Foam, 1/2", Top Hatch | 1 | ea | Up to 1" will work |
| PN789 | PIR Foam, 1/2", Top Outer | 1 | ea | Up to 1" will work |
| PN790 | PIR Foam, 1/2", Floor Access Panel, Rear | 1 | ea | Up to 1" will work |
| PN791 | PIR Foam, 1/2", Floor Access Panel, Front | 1 | ea | Up to 1" will work with some adjustments |
| PN792 | PIR Foam, 1/2", Side Floor Cover, Rear | 2 | ea | Up to 1" will work |
| PN793 | PIR Foam, 1/2", Side Floor Cover, Front | 2 | ea | Up to 1" will work |
| PN794 | PIR Foam, 1/2", Generic Side | 2 | ea | 3/8" thickness, at least 1/2" width. |
| PN797 | [Foam Weatherstrip, 3/4" x 3/8", 580mm](https://www.homedepot.com/p/M-D-Building-Products-3-8-in-x-10-ft-Black-Sponge-Rubber-Foam-Weatherstrip-Tape-06635/100353487) | 2 | ea |  |

## Misc

| ID | Description | UOM | Qty | Notes |
|:---|:---|----:|----:|:---|
| PN800 | [Vibration Damper, NEMA 17](https://www.amazon.com/BIGTREETECH-Direct-Vibration-Creality-Printers/dp/B083JTC6JJ) | 2 | ea |  |
| PN801 | [Heatsink, 42x42x12mm](https://www.amazon.com/BIGTREETECH-Direct-Vibration-Creality-Printers/dp/B083JTC6JJ) | 3 | ea | Z heatsinks optional |
| PN802 | [Heatsink, 14x14x6mm](https://www.amazon.com/ZZHXSM-Heatsink-Aluminum-Radiator-Conductive/dp/B092LW4K9L) | 1 | ea | For RPi, optional |
| PN810 | [Bed Spring](https://www.amazon.com/gp/product/B07SDFX766) | 4 | ea | Creality clone |
| PN811 | [Bed Leveling Nut, 60mm](https://www.amazon.com/gp/product/B07SDFX766) | 4 | ea | Creality clone |
| PN812 | [Heated Bed, 310x310mm](https://www.amazon.com/Creality-CR-10S-Aluminum-Heated-Replacement/dp/B07TVMGFRZ) | 1 | ea | Creality CR-10 Stock |
| PN813 | [Idler Pulley Plate](https://openbuildspartstore.com/idler-pulley-plate/) | 4 | ea | Or clone |
| PN814 | [Build Plate, Spring Steel, 310x310mm](https://www.amazon.com/gp/product/B07SH1S2C1) | 1 | ea |  |
| PN815 | [PTFE Tube, 4mm OD, 2mm ID](https://www.amazon.com/Teflon-tubing-Filament-Printer-Tech/dp/B073RDFTDV) | 1 | cm |  |
| PN816 | [French Press Filter, 4" (8 Cup)](https://www.amazon.com/gp/product/B08R8NQZG2) | 2 | ea |  |
| PN818 | [Silicone Tubing, 5/8" ID](https://www.amazon.com/gp/product/B08S3CXSRH) | 1 | cm | Quality varies, but 3/4" OD often comes out as 20mm |
| PN819 | [HEPA Cartridge, 72x20mm](https://www.amazon.com/gp/product/B07H7QWB2M) | 1 | ea | Vacuum filters for Kenmore EF-2 |
| PN821 | [Coupler, Pneumatic, PC4-M10](https://www.amazon.com/AiTrip-PC4-M10-Straight-Fitting-Extruder/dp/B07ZCNB1L8) | 2 | ea | Often found included with PTFE tube kits |
| PN823 | [Micro SD Card, Class A1](https://www.amazon.com/SanDisk-Extreme-microSDHC-UHS-3-SDSQXAF-032G-GN6MA) | 1 | ea | Class A1, 32GB |
| PN824 | [SD Card](https://www.amazon.com/Verbatim-Premium-Memory-UHS-I-Class/dp/B000RLBWJK) | 1 | ea | Any size works; solely for flashing MCU. |
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

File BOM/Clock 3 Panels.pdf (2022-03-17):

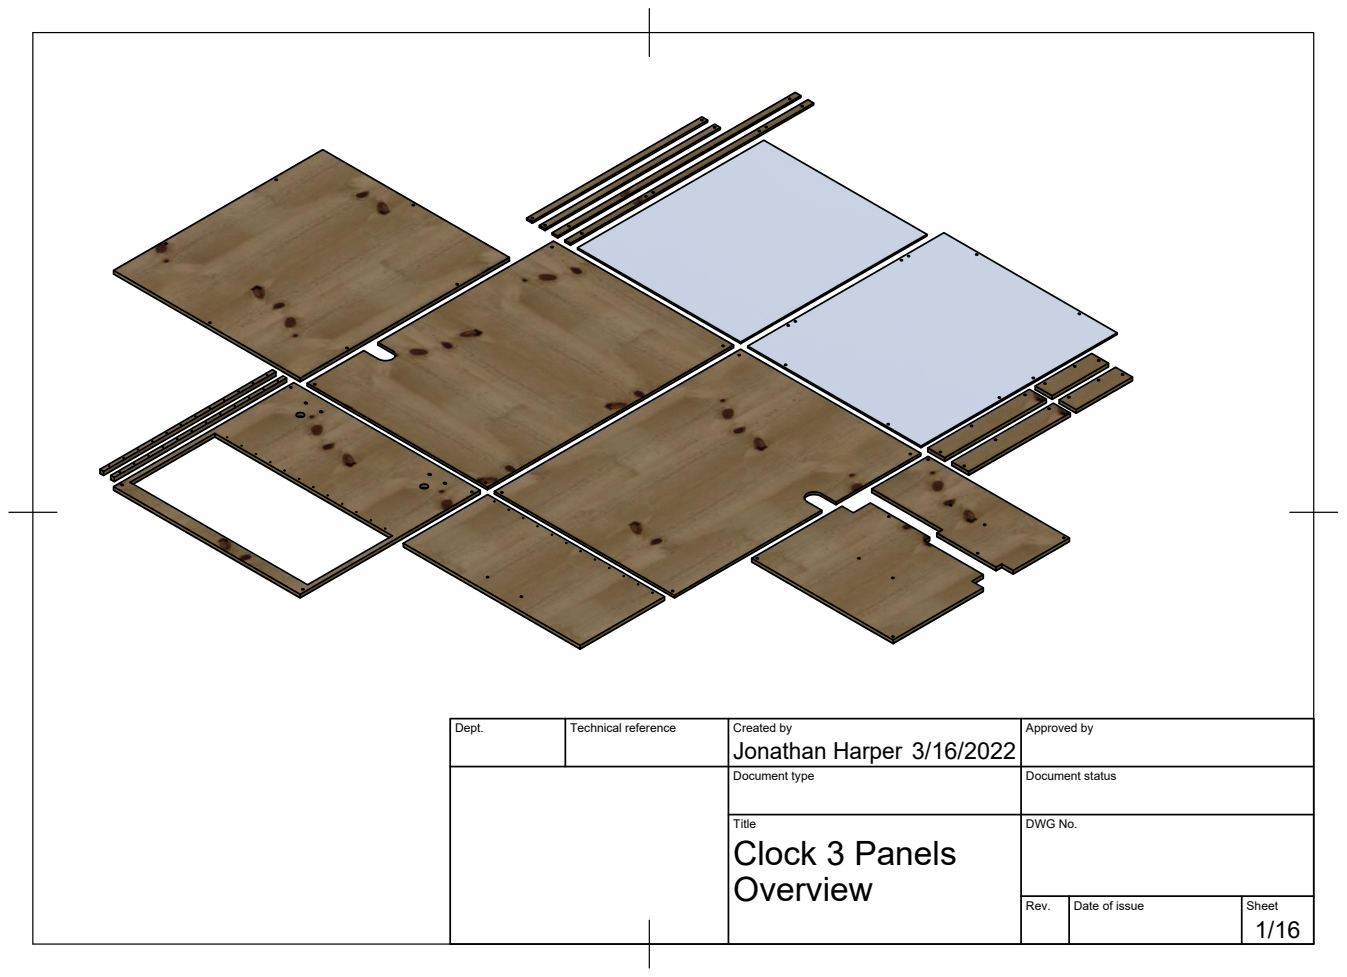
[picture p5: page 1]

Dept. | Technical reference | Created by Jonathan Harper 3/16/2022 | Approved by

Document type | Document status

Title Clock 3 Panels Overview | DWG No.

Rev. | Date of issue | Sheet

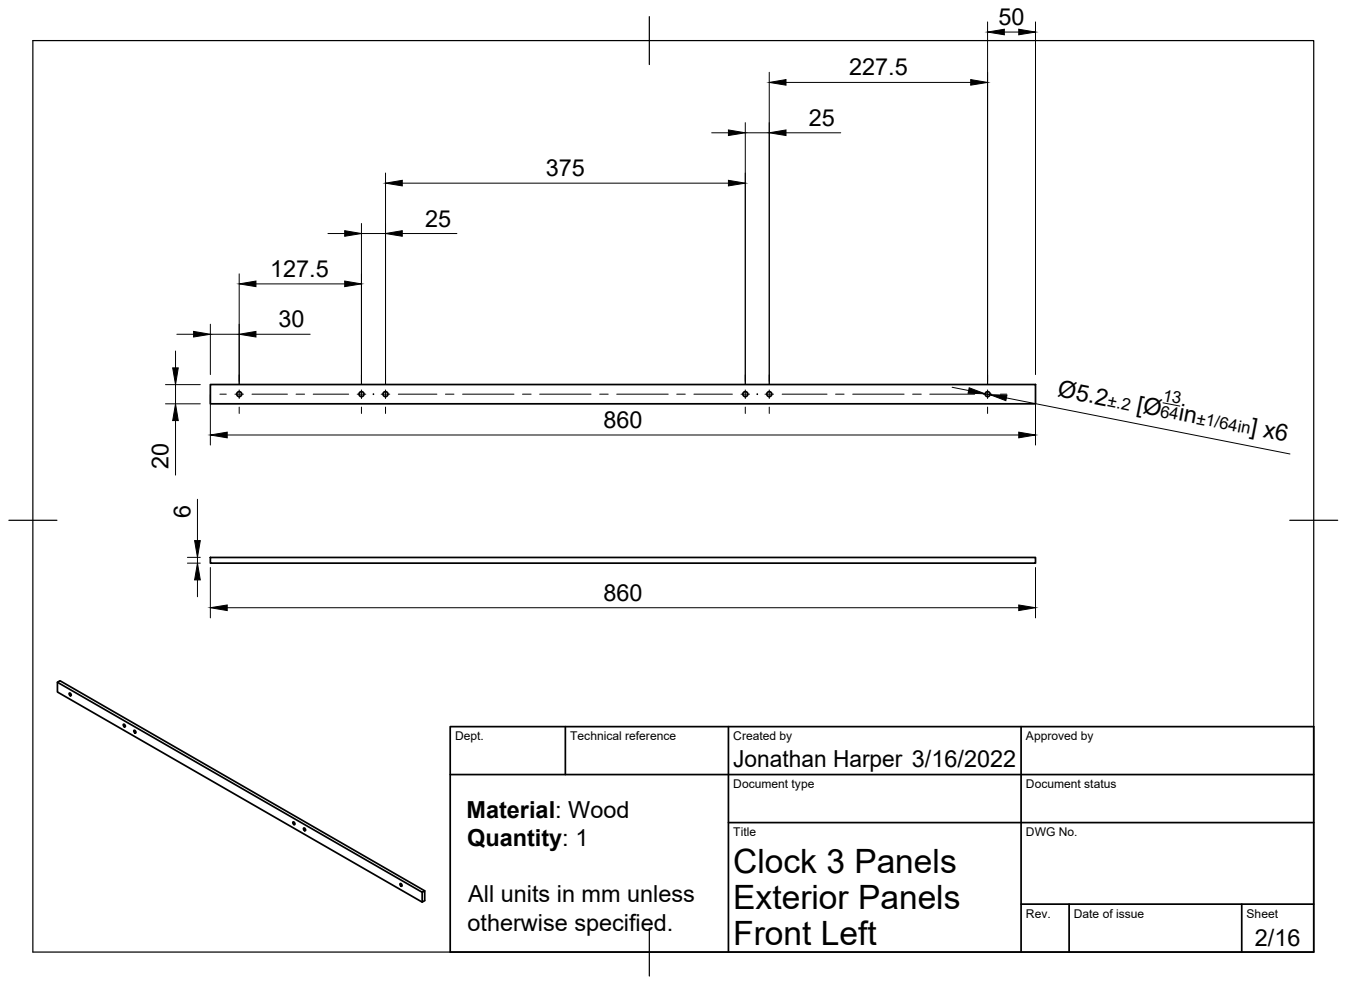
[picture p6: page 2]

Dept. | Technical reference | Created by Jonathan Harper 3/16/2022 | Approved by

Material: Wood Quantity: 1 All units in mm unless otherwise specified. | | Document type | Document status

Title Clock 3 Panels Exterior Panels Front Left | DWG No.

Rev. | Date of issue | Sheet

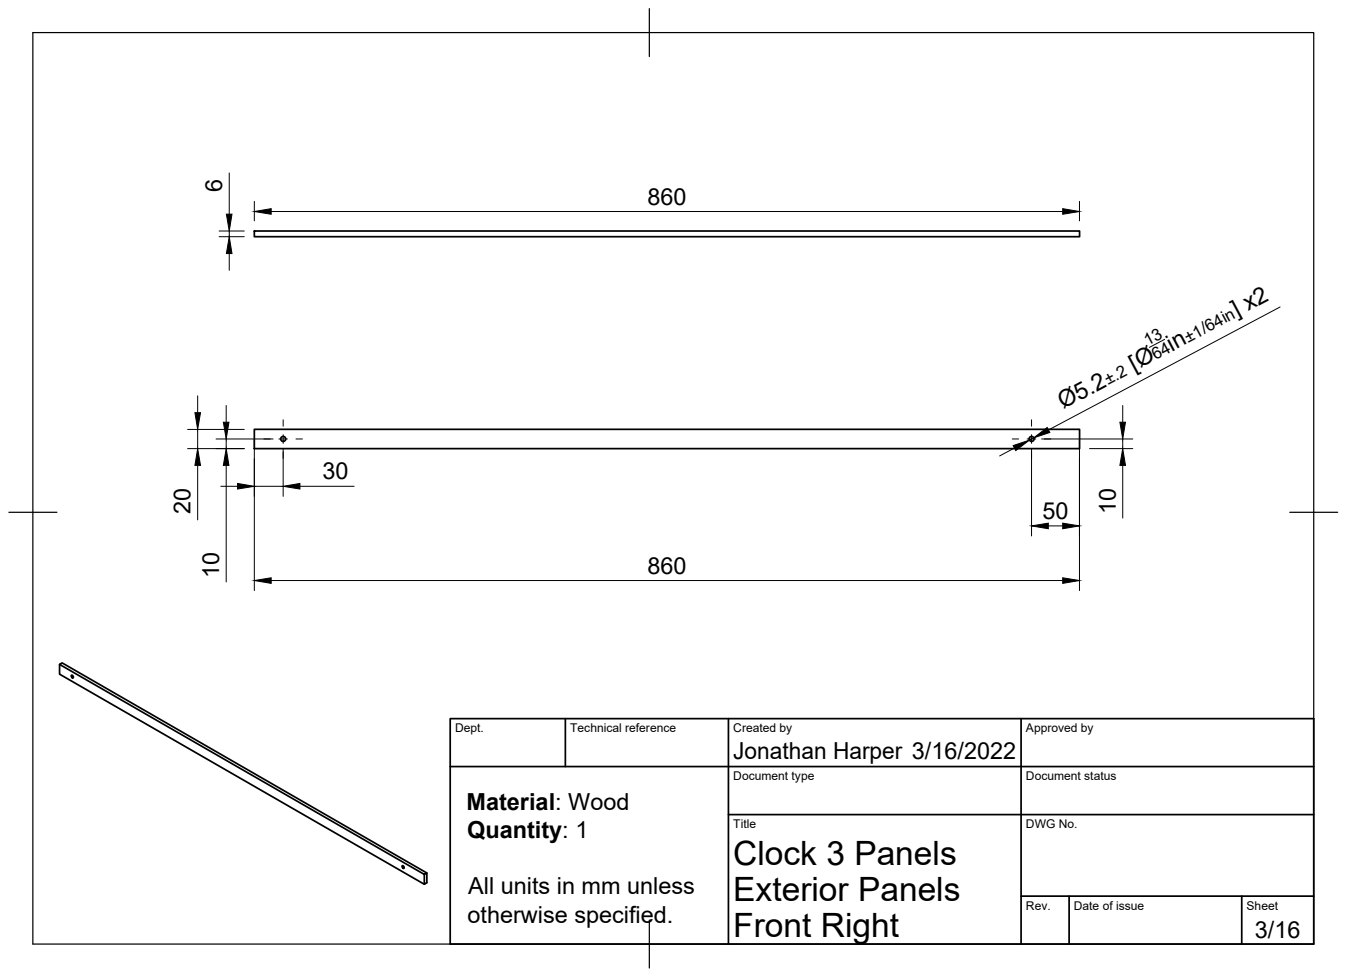
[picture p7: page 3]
Jonathan Harper 20

Dept. | Technical reference | Created by 3/16/2022 | Approved by

Material: Wood Quantity: 1 All units in mm unless | | Document type | Document status

Title Clock 3 Panels Exterior Panels Front Right | DWG No.

Rev. | Date of issue | Sheet

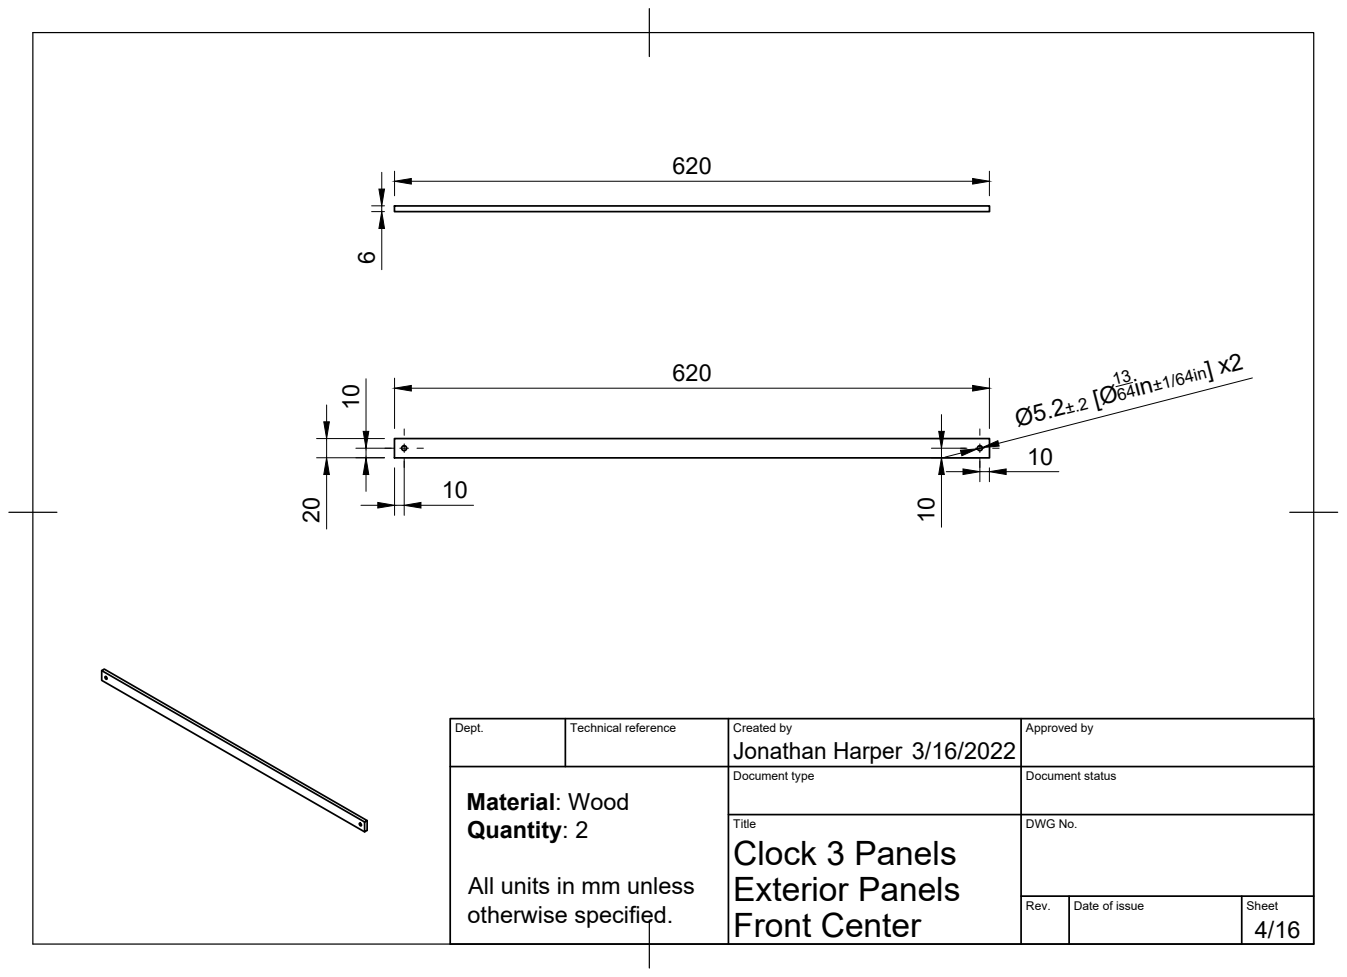
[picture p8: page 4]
Jonathan Harper 20

Dept. | Technical reference | Created by 3/16/2022 | Approved by

Material: Wood Quantity: 2 All units in mm unless | | Document type | Document status

Title Clock 3 Panels Exterior Panels Front Center | DWG No.

Rev. | Date of issue | Sheet

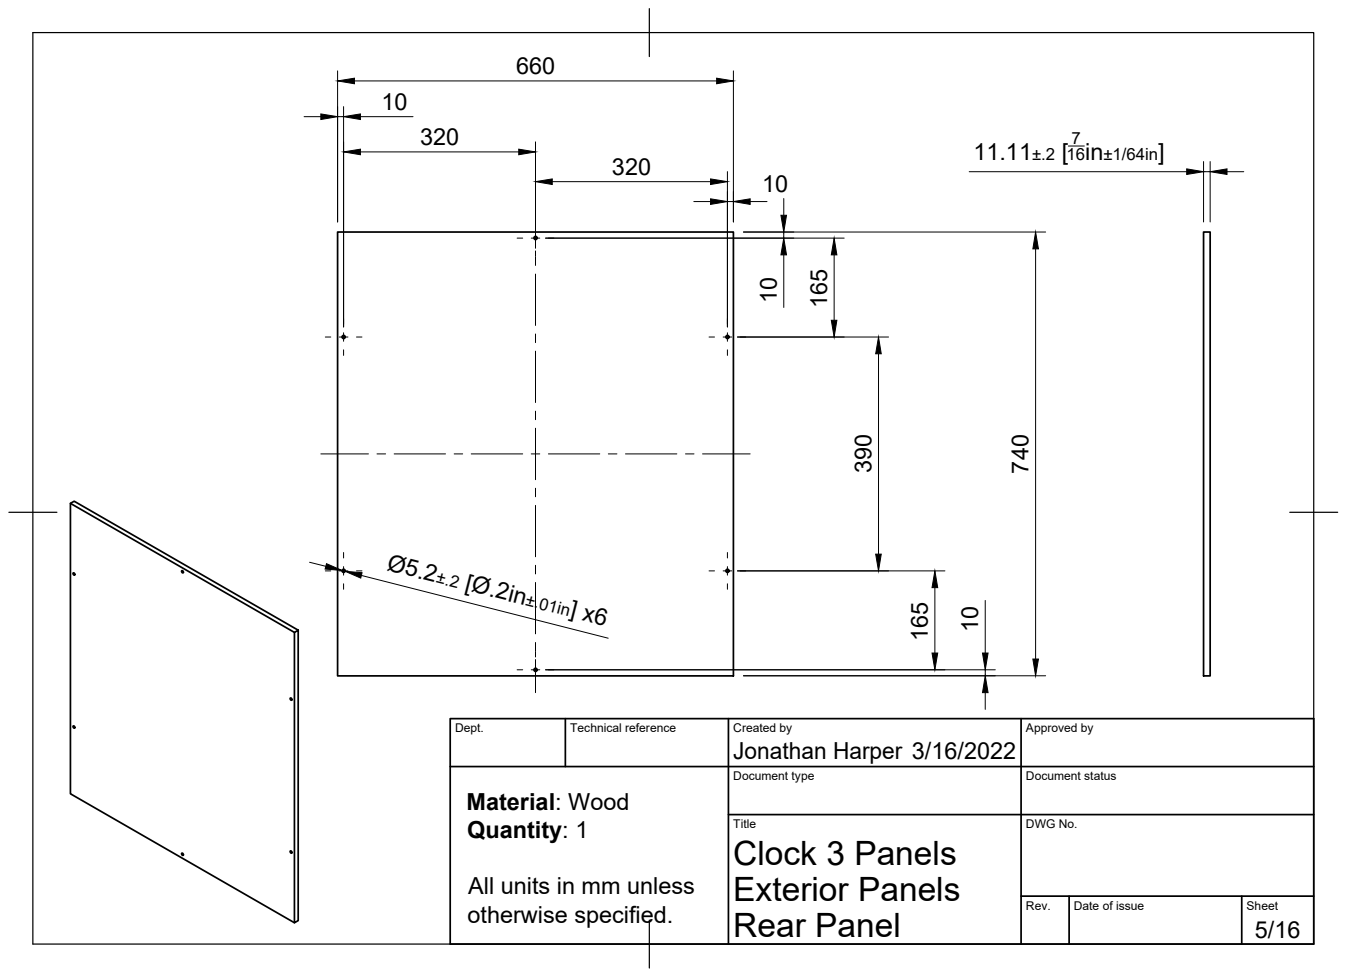
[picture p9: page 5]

Dept. | Technical reference | Created by Jonathan Harper 3/16/2022 | Approved by

Material: Wood Quantity: 1 All units in mm unless | | Document type | Document status

Title Clock 3 Panels Exterior Panels Rear Panel | DWG No.

Rev. | Date of issue | Sheet

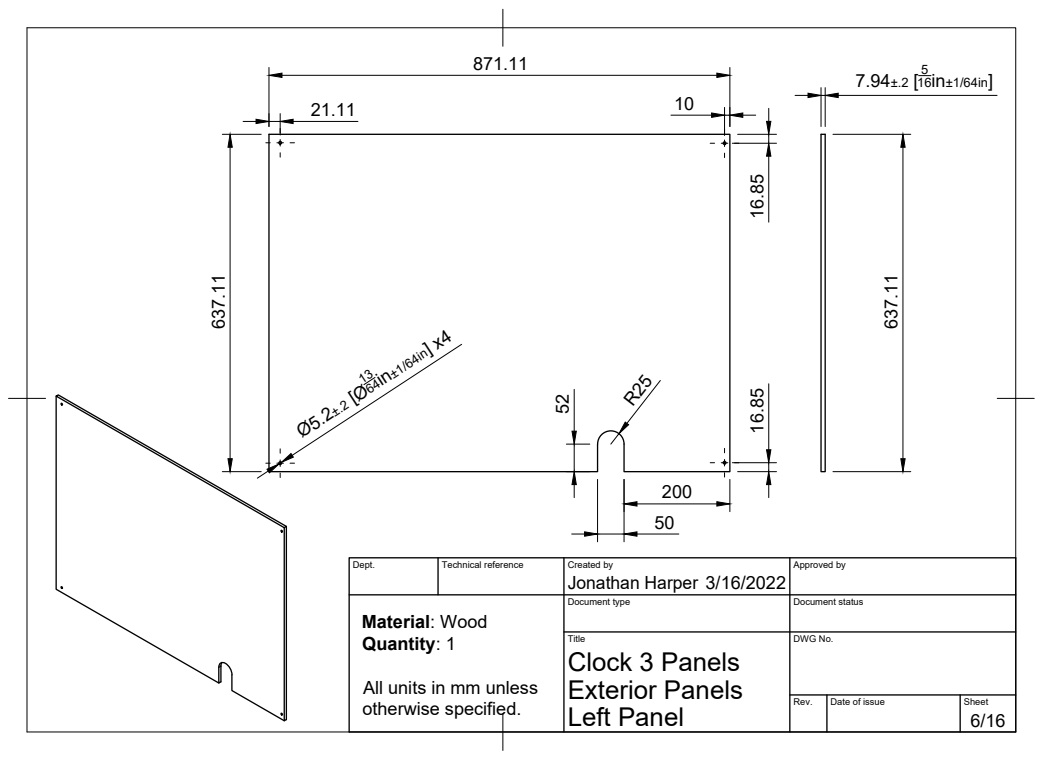
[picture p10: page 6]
otherwise specified.

Dept. | Technical reference | Created by Jonathan Harper 3/16/2022 | Approved by

Material: Wood Quantity: 1 All units in mm unless | | Document type | Document status

Title Clock 3 Panels Exterior Panels Left Panel | DWG No.

Rev. | Date of issue | Sheet

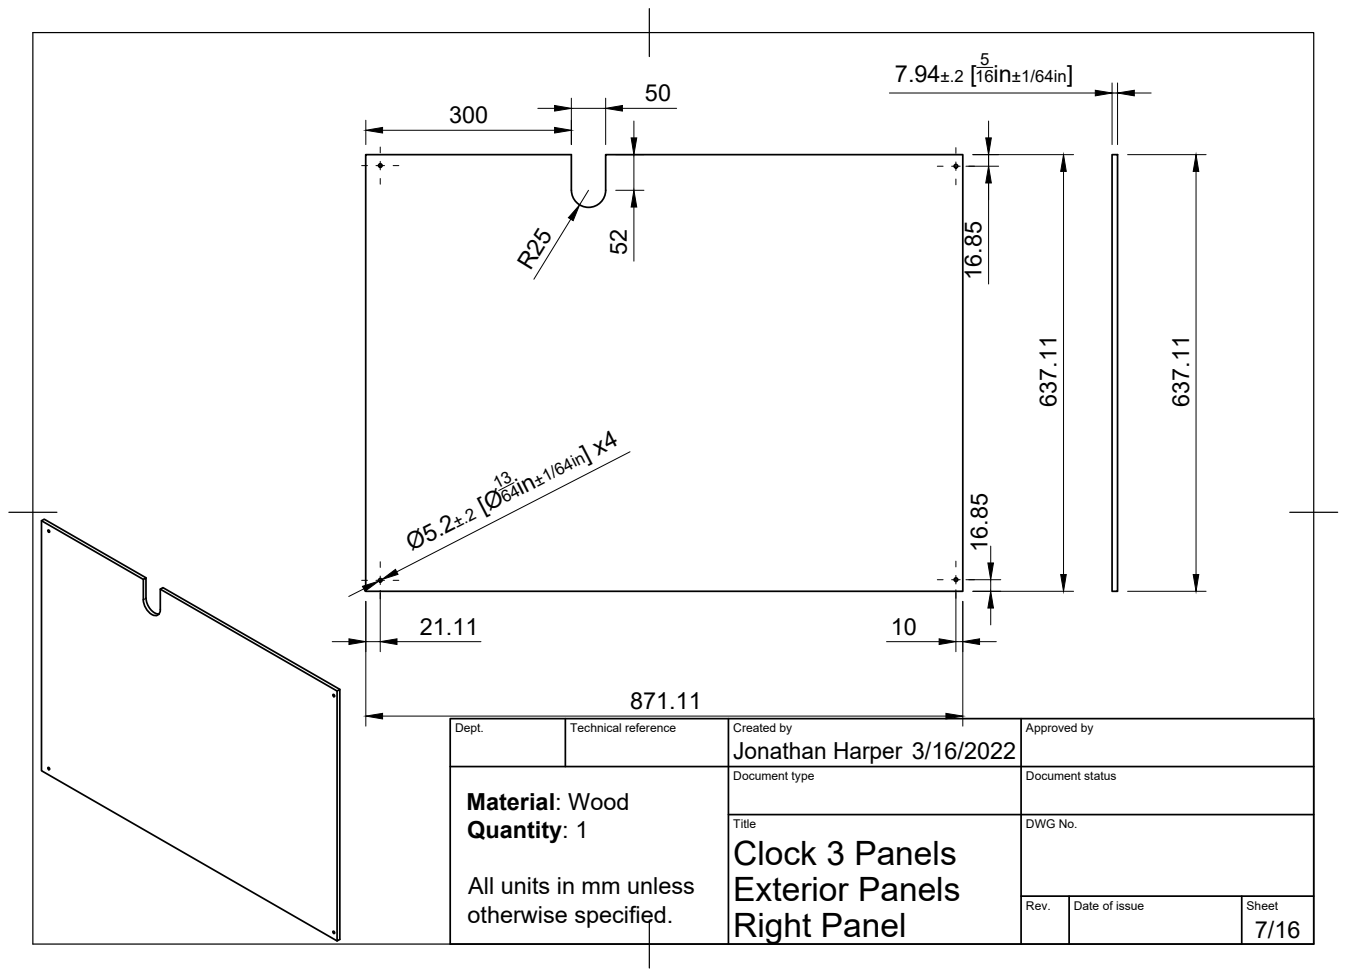
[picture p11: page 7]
Jonathan Harper

Dept. | Technical reference | Created by 3/16/2022 | Approved by

Material: Wood Quantity: 1 All units in mm unless | | Document type | Document status

Title Clock 3 Panels Exterior Panels Right Panel | DWG No.

Rev. | Date of issue | Sheet

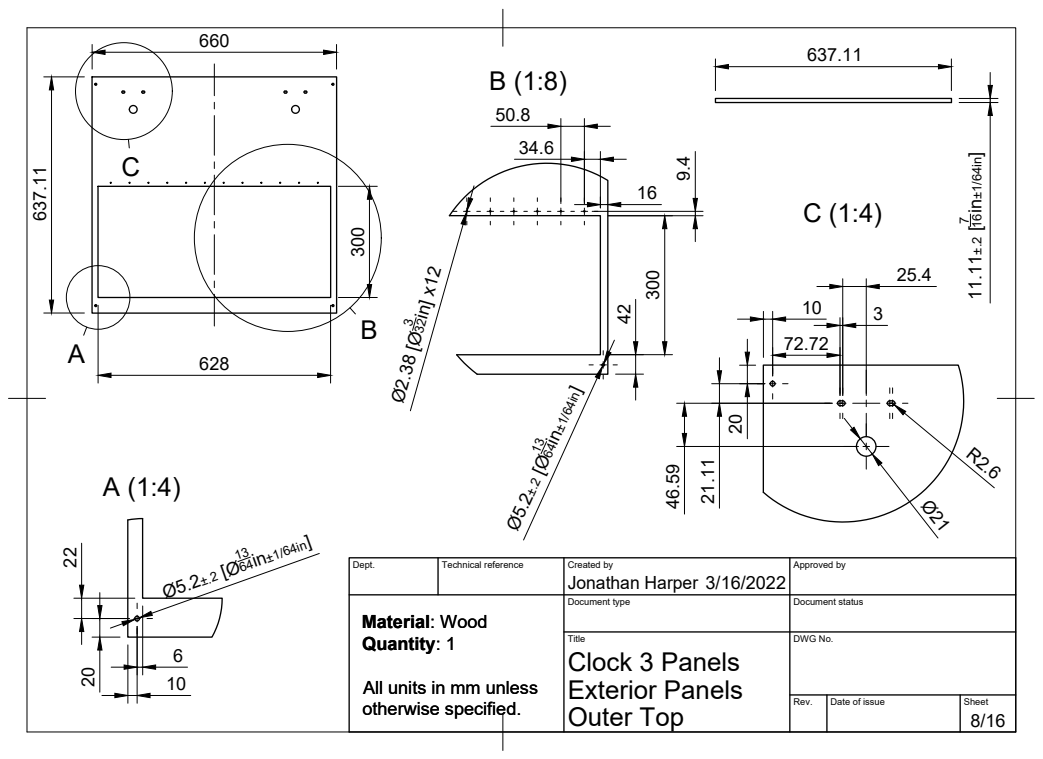
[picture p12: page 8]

Dept. | Technical reference | Created by Jonathan Harper 3/16/2022 | Approved by

Material: Wood Material: Wood Quantity: 1 Quantity: 1 All units in mm unless All units in mm unless | | Document type | Document status

Title Clock 3 Panels Exterior Panels Outer Top | DWG No.

Rev. | Date of issue | Sheet


Dept. | Technical reference | Created by Jonathan Harper 3/16/2022 | Approved by

Material: Wood Quantity: 1 All units in mm unless | | Document type | Document status

Title Clock 3 Panels Exterior Panels Top Hatch | DWG No.

Rev. | Date of issue | Sheet


Dept. | Technical reference | Created by Jonathan Harper 3/16/2022 | Approved by

Material: Wood Quantity: 2 All units in mm unless | | Document type | Document status

Title Clock 3 Panels Exterior Panels Hinge Screw Anchor | DWG No.

Rev. | Date of issue | Sheet


Dept. | Technical reference | Created by Jonathan Harper 3/16/2022 | Approved by

Material: Wood Quantity: 2 All units in mm unless | | Document type | Document status

Title Clock 3 Panels Floor Panels Front Side Cover | DWG No.

Rev. | Date of issue | Sheet

otherwise specified. 59.75

Dept. | Technical reference | Created by Jonathan Harper 3/16/2022 | Approved by

Material: Wood Quantity: 2 All units in mm unless | | Document type | Document status

Title Clock 3 Panels Floor Panels Rear Side Cover | DWG No.

Rev. | Date of issue | Sheet


Dept. | Technical reference | Created by Jonathan Harper 3/16/2022 | Approved by

Material: Wood Quantity: 1 All units in mm unless | | Document type | Document status

Title Clock 3 Panels Floor Panels Front Access Panel | DWG No.

Rev. | Date of issue | Sheet


Dept. | Technical reference | Created by Jonathan Harper 3/16/2022 | Approved by

Material: Wood Quantity: 1 All units in mm unless | | Document type | Document status

Title Clock 3 Panels Floor Panels Rear Access Panel | DWG No.

Rev. | Date of issue | Sheet


Dept. | Technical reference | Created by Jonathan Harper 3/16/2022 | Approved by

Material: Clear Acrylic Quantity: 1 All units in mm unless | | Document type | Document status

Title Clock 3 Panels Door Panels Interior Panel | DWG No.

Rev. | Date of issue | Sheet


Dept. | Technical reference | Created by Jonathan Harper 3/16/2022 | Approved by

Material: Clear Acrylic Quantity: 1 All units in mm unless | | Document type | Document status

Title Clock 3 Panels Door Panels Exterior Panel | DWG No.

Rev. | Date of issue | Sheet

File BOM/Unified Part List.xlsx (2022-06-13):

ID | Type | Description | UOM | DefaultValue | RefSupplier | RefUrl | RefMfgr | RefMfgrPN | Notes
MN001 | Materials | Activated Carbon, Virgin Coconut, 4x8 | lb | 1 | Amazon | https://www.amazon.com/gp/product/B00XIIH43W | EnviroSupply |  | 0.5lb to start; have heard mixed reviews of this supplier via Amazon
MN002 | Materials | Thermal Glue | ea | 1 | Amazon | https://www.amazon.com/gp/product/B07TSH6MNT | GENNEL
MN003 | Materials | VHB Tape, Double-Sided, 1in Width | ft | 15 | Amazon | https://www.amazon.com/gp/product/B07K4PQG8P | 3M
MN004 | Materials | Zip ties, 4" | pk | 1 | Amazon | https://www.amazon.com/AmazonBasics-Multi-Purpose-Cable-Ties-200-Piece/dp/B087MKMSDY | Generic |  | Qty varies based on cofiguration and personal preference
MN010 | Materials | Filament, ABS | kg | 2 | Atomic Filament | https://atomicfilament.com/collections/abs-3d-filament/products/glossy-black-abs-pro-m94-filament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 | Atomic |  | Estimate
MN011 | Materials | Filament, TPU, 95A | kg | 1 | MatterHackers | https://www.matterhackers.com/store/l/black-mh-build-series-tpu-filament-175mm-1kg/sk/MP6A4G56 |  |  | Even 250g is probably enough; 500g is definitely enough.
MN100 | Materials | Polyisocyanurate Foam, 1/2", 4'x8' sheet | ea | 1 | Home Depot | https://www.homedepot.com/p/RMAX-Pro-Select-R-Matte-Plus-3-1-2-in-x-4-ft-x-8-ft-R-3-2-Foam-Insulation-Board-637902/313501506 | RMAX | R-Matte Plus-3 | Can substitute 3/4" and 1" in places for better insulation
MN101 | Materials | Plywood sheet, 12mm thickness, 4'x5' | ea | 2 | Locally Sourced |  |  |  | For paneling
MN102 | Materials | Acrylic sheet, 3mm thickness, 4'x5' | ea | 1 | Locally Sourced |  |  |  | For door windows
MN103 | Materials | Plywood sheet, 6mm thickness, 4'x5' | ea | 1 | Locally Sourced |  |  |  | For front panels
MN104 | Materials | Wire loom, PET, 1/4" | cm | 260 | Amazon | https://www.amazon.com/gp/product/B08D3RXL7T | Generic |  | Minimum quantity. More cables can be wrapped.
MN105 | Materials | Wire loom, PET, 1/2" | cm | 120 | Amazon | https://www.amazon.com/gp/product/B08D3RXL7T | Generic
MN107 | Materials | Heat shrink tubing, various sizes | pk | 1 | Amazon | https://www.amazon.com/gp/product/B07WWWPR2X | Generic |  | 2.5mm - 4mm, mostly
MN108 | Materials | Heat shrink tubing, 13mm | cm | 45 | Amazon | https://www.amazon.com/XHF-Inch-13mm-Waterproof-Insulation/dp/B07FPDBGYH | Generic |  | For PET loom ends
MN110 | Materials | Hookup Wire, Silicone, 16 AWG | cm | 625 | Amazon | https://www.amazon.com/Electrical-Gauge-Silicone-Cable-Black/dp/B0746HRVZP | Generic |  | Red, black and optionally green or yellow
MN111 | Materials | Hookup Wire, Silicone, 20 AWG | cm | 520 | Amazon | https://www.amazon.com/gp/product/B07T4SYVYG | Generic |  | Red, black
MN112 | Materials | Hookup Wire, Silicone, 24 AWG | cm | 8820 | Amazon | https://www.amazon.com/gp/product/B087TJNJZS/ | Generic |  | OR 26 awg
MN113 | Materials | Hookup Wire, Silicone, 12 AWG | cm | 60 | Amazon | https://www.amazon.com/BNTECHGO-Silicone-Flexible-Strands-Stranded/dp/B01AQU3ST8 | Generic |  | OR 13 awg; red and black
MN201 | Materials | JST SM Contact Pin | ea | 88 | Digikey | https://www.digikey.com/en/products/detail/jst-sales-america-inc/SYM-001T-P0-6-N/1465026 | JST | SYM-001T-P0.6(N)
MN201 | Materials | JST SM Pin Socket | ea | 88 | Digikey | https://www.digikey.com/en/products/detail/jst-sales-america-inc/SYF-001T-P0-6-LF-SN/2027280 | JST | SYF-001T-P0.6(LF)(SN)
MN202 | Materials | JST SM Connector, 2.54mm, Male, 2 Pin | ea | 12 | Digikey | https://www.digikey.com/en/products/detail/jst-sales-america-inc/SMR-02V-B/764265 | JST | SMR-02V-B
MN203 | Materials | JST SM Connector, 2.54mm, Male, 3 Pin | ea | 10 | Digikey | https://www.digikey.com/en/products/detail/jst-sales-america-inc/SMR-03V-B/5702345 | JST | SMR-03V-B
MN204 | Materials | JST SM Connector, 2.54mm, Male, 4 Pin | ea | 6 | Digikey | https://www.digikey.com/en/products/detail/jst-sales-america-inc/SMR-04V-B/2137107 | JST | SMR-04V-B
MN205 | Materials | JST SM Connector, 2.54mm, Male, 5 Pin | ea | 2 | Digikey | https://www.digikey.com/en/products/detail/jst-sales-america-inc/smr-05v-b/3622430 | JST | SMR-05V-B
MN210 | Materials | JST SM Connector, 2.54mm, Female, 2 Pin | ea | 12 | Digikey | https://www.digikey.com/en/products/detail/jst-sales-america-inc/SMP-02V-BC/1835574 | JST | SMP-02V-BC
MN211 | Materials | JST SM Connector, 2.54mm, Female, 3 Pin | ea | 10 | Digikey | https://www.digikey.com/en/products/detail/jst-sales-america-inc/SMP-03V-BC/2514249 | JST | SMP-03V-BC
MN212 | Materials | JST SM Connector, 2.54mm, Female, 4 Pin | ea | 6 | Digikey | https://www.digikey.com/en/products/detail/jst-sales-america-inc/SMP-04V-BC/7230521 | JST | SMP-04V-BC
MN213 | Materials | JST SM Connector, 2.54mm, Female, 5 Pin | ea | 2 | MISUMI USA | https://us.misumi-ec.com/vona2/detail/222000498388/?HissuCode=SMP-05V-BC | JST | SMP-05V-BC | Digikey doesn't carry this, for some reason
MN220 | Materials | JST XH Pin Socket | ea | 55 | Digikey | https://www.digikey.com/en/products/detail/jst-sales-america-inc/SXH-002T-P0-6/1651063 | JST | SXH-002T-P0.6
MN221 | Materials | JST XH Connector, 2.5mm, Female, 2 Pin | ea | 6 | Digikey | https://www.digikey.com/en/products/detail/jst-sales-america-inc/XHP-2/555485 | JST | XHP-2
MN222 | Materials | JST XH Connector, 2.5mm, Female, 3 Pin | ea | 9 | Digikey | https://www.digikey.com/en/products/detail/jst-sales-america-inc/XHP-3/1651017 | JST | XHP-3
MN223 | Materials | JST XH Connector, 2.5mm, Female, 4 Pin | ea | 3 | Digikey | https://www.digikey.com/en/products/detail/jst-sales-america-inc/XHP-4/683353 | JST | XHP-4
MN240 | Materials | JST PH Connector, 2.0mm, Female, 6 Pin | ea | 3 | Digikey | https://www.digikey.com/en/products/detail/adafruit-industries-llc/4422/11497499 | JST | (D)PHR-6(L) | Only needed if steppers have integrated connectors
MN241 | Materials | JST PH Pin Socket | ea | 12 | Digikey | https://www.digikey.com/en/products/detail/adafruit-industries-llc/4422/11497499 | JST | SPH-004T-P0.5S | Only needed if steppers have integrated connectors
MN242 | Materials | XT 60 Connector Set, 12 awg 150mm pigtails | pk | 1 | Amazon | https://www.amazon.com/gp/product/B073QJWVVK/ | Generic |  | Optional
MN250 | Materials | Ring Connector, 18-24 awg | ea | 3 |  |  | Generic |  | Number varies based on configuration
MN251 | Materials | Ring Connector, 14-18 awg | ea | 9 |  |  | Generic |  | Number varies based on configuration
MN252 | Materials | Spade Connector, 14-18 awg | ea | 5 |  |  | Generic
MN253 | Materials | Butt Splice, 12-14 awg | ea | 4 |  |  | Generic |  | Without XT60, only two needed.
MN260 | Materials | Micro Fit 3 Connector Pin | ea | 4 | Digikey | https://www.digikey.com/en/products/detail/molex/0430310009/252485 | Molex | 430310009
MN261 | Materials | Micro Fit 3 Connector Socket | ea | 4 | Digikey | https://www.digikey.com/en/products/detail/molex/0430300009/252481 | Molex | 430300009
MN262 | Materials | Micro Fit 3 Connector, 2 pin, 2 Row, Male | ea | 2 | Digikey | https://www.digikey.com/en/products/detail/molex/0430250200/252496 | Molex | 430250200
MN263 | Materials | Micro Fit 3 Connector, 2 pin, 2 Row, Panel Mount | ea | 2 | Digikey | https://www.digikey.com/en/products/detail/molex/0430200200/252490 | Molex | 430200200
PN001 | Printed | XY Pulleys, L Bottom | ea |  | Printed | 001 - XY Pulleys, L Bottom.stl |  | 001
PN002 | Printed | XY Pulleys, L Top | ea |  | Printed | 002 - XY Pulleys, L Top.stl |  | 002
PN003 | Printed | XY Pulleys, R Bottom | ea |  | Printed | 003 - XY Pulleys, R Bottom.stl |  | 003
PN004 | Printed | XY Pulleys, R Top | ea |  | Printed | 004 - XY Pulleys, R Top.stl |  | 004
PN005 | Printed | XY Joint, L Top | ea |  | Printed | 005 - XY Joint, L Top.stl |  | 005
PN006 | Printed | XY Joint, L Mid | ea |  | Printed | 006 - XY Joint, L Mid.stl |  | 006
PN007 | Printed | XY Joint, L Bottom | ea |  | Printed | 007 - XY Joint, L Bottom.stl |  | 007
PN008 | Printed | XY Joint, R Top | ea |  | Printed | 008 - XY Joint, R Top.stl |  | 008
PN009 | Printed | XY Joint, R Mid | ea |  | Printed | 009 - XY Joint, R Mid.stl |  | 009
PN010 | Printed | XY Joint, R Bottom | ea |  | Printed | 010 - XY Joint, R Bottom.stl |  | 010
PN011 | Printed | XY Tensioner, Bolt Receiver | ea |  | Printed | 011 - XY Tensioner, Bolt Receiver.stl |  | 011
PN012 | Printed | XY Tensioner, Idler Seat | ea |  | Printed | 012 - XY Tensioner, Idler Seat.stl |  | 012
PN013 | Printed | XY Tensioner, Tensioner Cap | ea |  | Printed | 013 - XY Tensioner, Tensioner Cap.stl |  | 013
PN014 | Printed | XY Tensioner, Guide Frame | ea |  | Printed | 014 - XY Tensioner, Guide Frame.stl |  | 014
PN015 | Printed | XY Steppers, Vibration Damper, TPU | ea |  | Printed | 015 - XY Steppers, Vibration Damper, TPU.stl |  | 015 | No ID tag
PN016 | Printed | XY Steppers, Stepper Mount | ea |  | Printed | 016 - XY Steppers, Stepper Mount.stl |  | 016
PN017 | Printed | XY Motion, L Y Rail Guide | ea |  | Printed | 017 - XY Motion, L Y Rail Guide.stl |  | 017
PN018 | Printed | XY Motion, R Y Rail Guide | ea |  | Printed | 018 - XY Motion, R Y Rail Guide.stl |  | 018 | Also acts as limit switch mount
PN019 | Printed | Z Motion, Lower Rail Bracket | ea |  | Printed | 019 - Z Motion, Lower Rail Bracket.stl |  | 019
PN020 | Printed | Z Axis, Bed Corner Bracket | ea |  | Printed | 020 - Z Axis, Bed Corner Bracket.stl |  | 020
PN021 | Printed | Z Axis, L Gantry | ea |  | Printed | 021 - Z Axis, L Gantry.stl |  | 021
PN022 | Printed | Z Axis, R Gantry | ea |  | Printed | 022 - Z Axis, R Gantry.stl |  | 022
PN023 | Printed | Z Axis, L Stepper Mount | ea |  | Printed | 023 - Z Axis, L Stepper Mount.stl |  | 023
PN024 | Printed | Z Axis, R Stepper Mount | ea |  | Printed | 024 - Z Axis, R Stepper Mount.stl |  | 024
PN025 | Printed | Z Motion, L Limit Switch Mount | ea |  | Printed | 025 - Z Motion, L Limit Switch Mount.stl |  | 025
PN026 | Printed | Z Motion, R Limit Switch Mount | ea |  | Printed | 026 - Z Motion, R Limit Switch Mount.stl |  | 026
PN027 | Printed | Z Axis, L Lead Screw Plate | ea |  | Printed | 027 - Z Axis, L Lead Screw Plate.stl |  | 027
PN028 | Printed | Z Axis, R Lead Screw Plate | ea |  | Printed | 028 - Z Axis, R Lead Screw Plate.stl |  | 028
PN029 | Printed | Z Axis, Bed Wire Support | ea |  | Printed | 029 - Z Axis, Bed Wire Support.stl |  | 029
PN030 | Printed | X Gantry, Carriage Mount | ea |  | Printed | 030 - X Gantry, Carriage Mount.stl |  | 030
PN031 | Printed | X Gantry, Top Mount | ea |  | Printed | 031 - X Gantry, Top Mount.stl |  | 031
PN032 | Printed | X Gantry, Back Mount | ea |  | Printed | 032 - X Gantry, Back Mount.stl |  | 032
PN033 | Printed | X Gantry, Front Mount | ea |  | Printed | 033 - X Gantry, Front Mount.stl |  | 033
PN034 | Printed | X Gantry, L Belt Clamp | ea |  | Printed | 034 - X Gantry, L Belt Clamp.stl |  | 034 | No ID tag
PN035 | Printed | X Gantry, R Belt Clamp | ea |  | Printed | 035 - X Gantry, R Belt Clamp.stl |  | 035 | No ID tag
PN040 | Printed | Toolhead, Hotend Mounting Bracket | ea |  | Printed | 040 - Toolhead, Hotend Mounting Bracket.stl |  | 040 | No ID tag
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

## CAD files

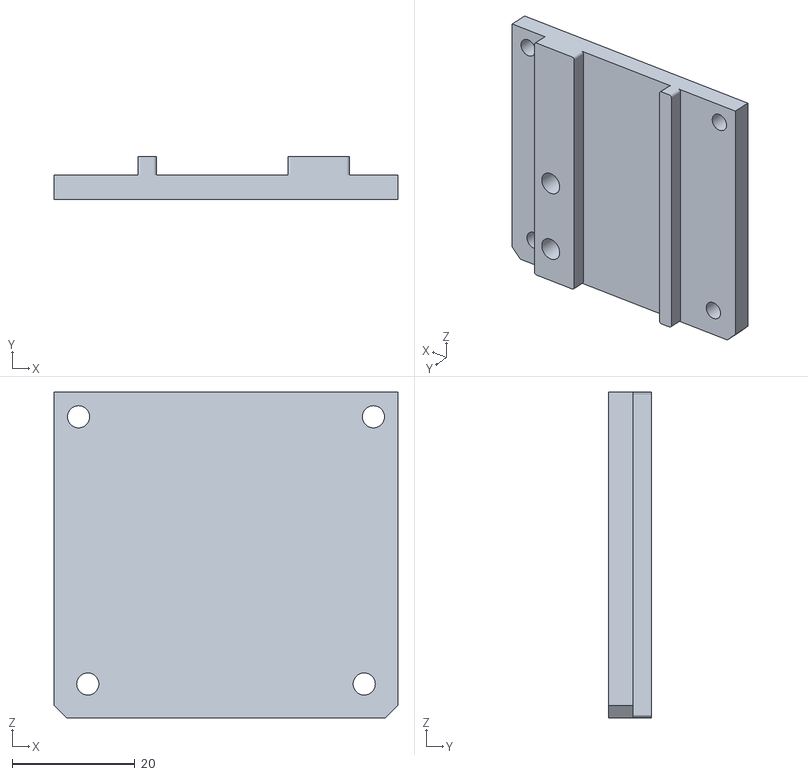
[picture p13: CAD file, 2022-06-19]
STL/032 - X Gantry, Back Mount.stl
56.0 x 7.00 x 53.0

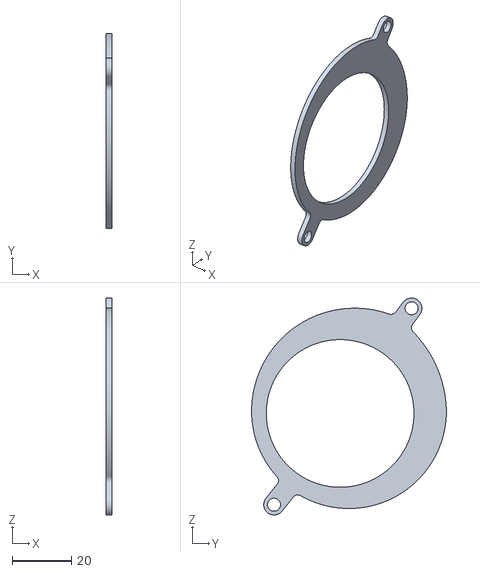
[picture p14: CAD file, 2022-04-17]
STL/Filtration/201 - Filtration, Fan Intake Gasket, TPU.stl
2.00 x 66.0 x 73.5

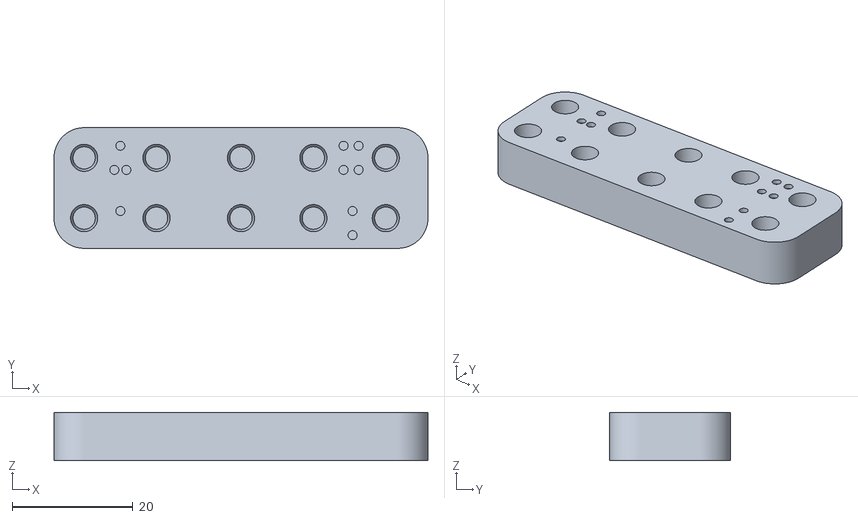
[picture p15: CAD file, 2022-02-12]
STL/Heat Sert Insert Tools/M3 Heat Set Insert Practice Block.stl
62.0 x 20.0 x 8.00

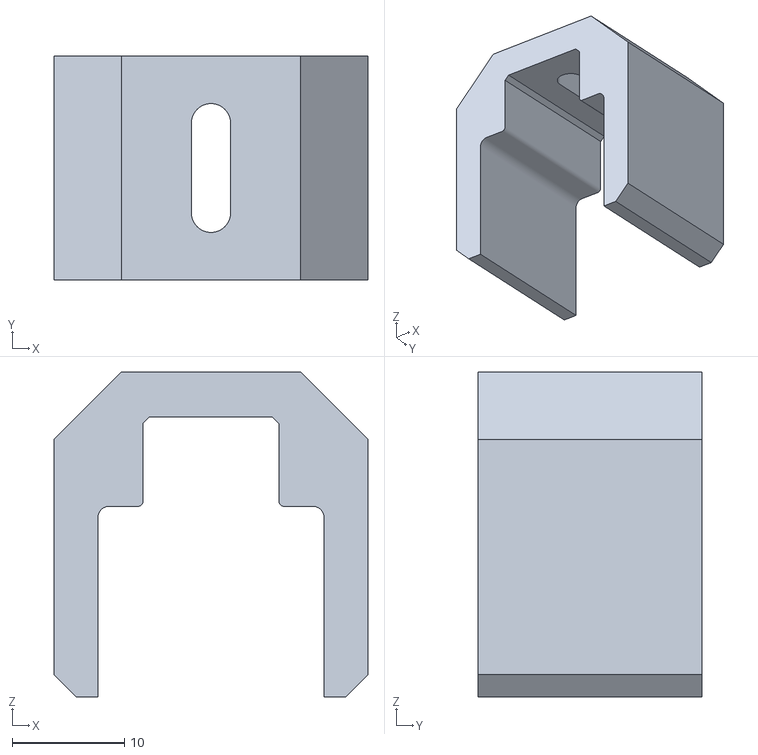
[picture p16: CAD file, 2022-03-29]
STL/Linear Rail Tools/Centering Guide.stl
28.0 x 20.0 x 29.0

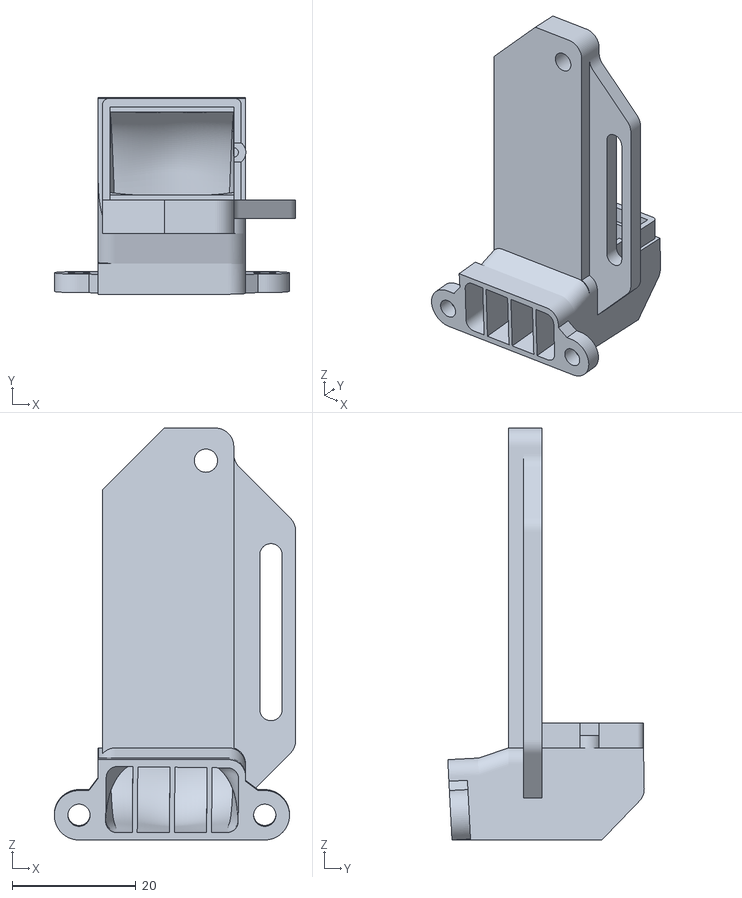
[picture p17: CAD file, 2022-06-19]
STL/045 - Toolhead, Part Fan Mount.stl
39.0 x 31.7 x 66.5

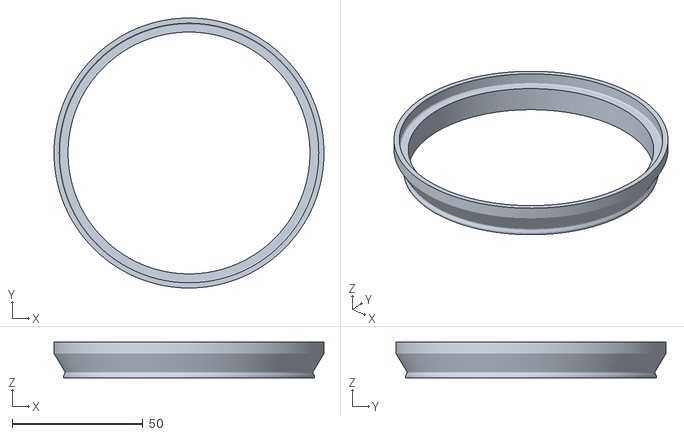
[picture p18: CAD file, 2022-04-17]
STL/Filtration/206 - Filtration, AC Tank Gasket, TPU.stl
103.1 x 103.1 x 13.6

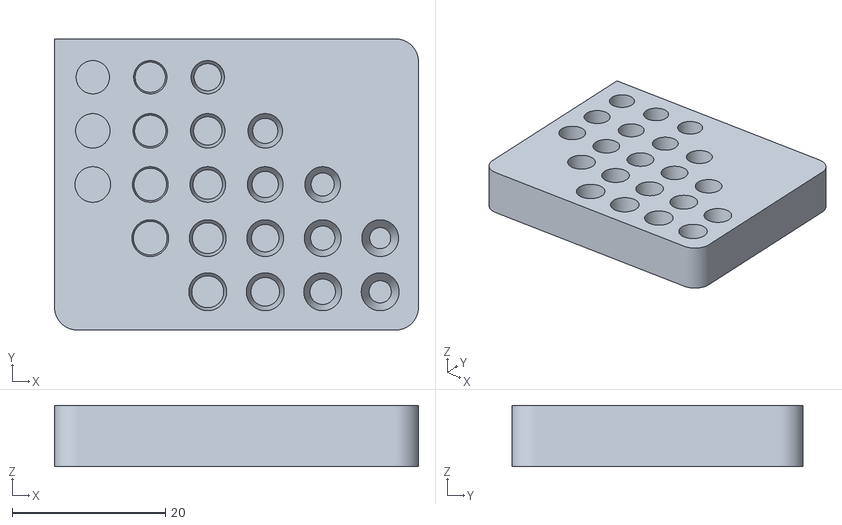
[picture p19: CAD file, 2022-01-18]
STL/Heat Sert Insert Tools/M3 Heat Set Insert Parameter Block.stl
47.5 x 38.0 x 8.00

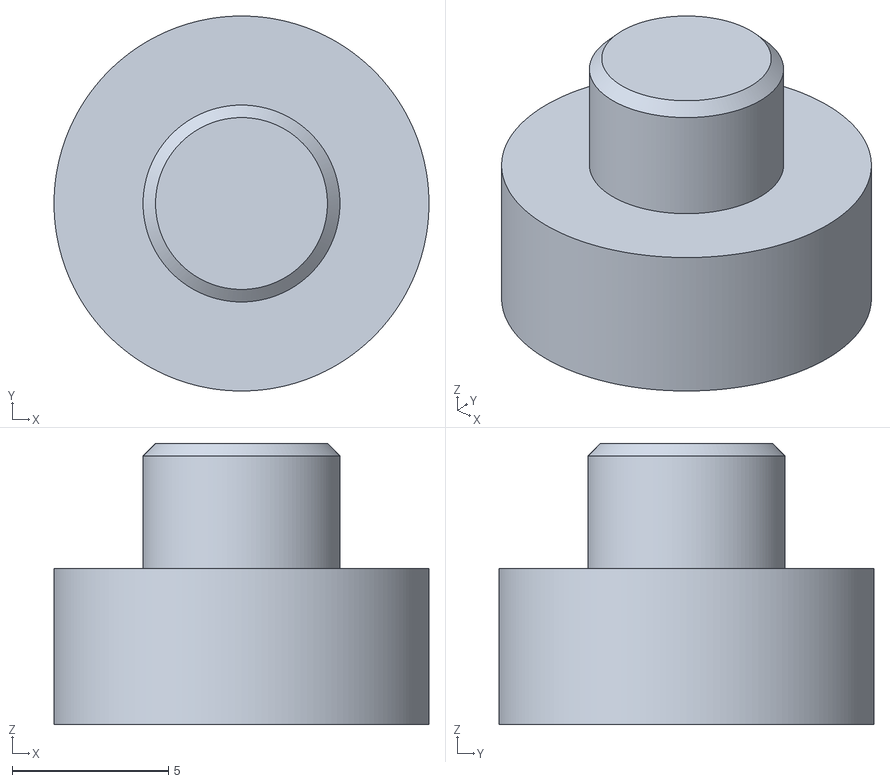
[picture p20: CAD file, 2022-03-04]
STL/Linear Rail Tools/Linear Rail Plug (TPU).stl
12.0 x 12.0 x 9.00

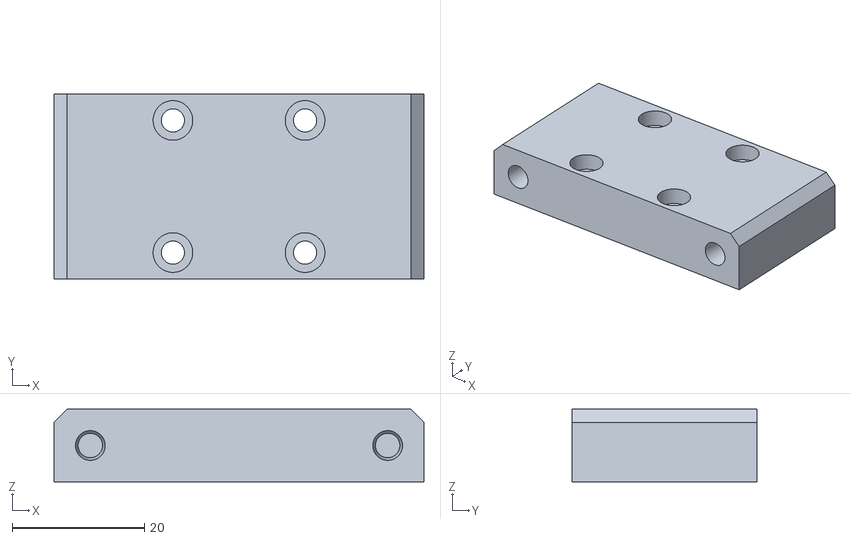
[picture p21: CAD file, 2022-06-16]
STL/030 - X Gantry, Carriage Mount.stl
56.0 x 28.0 x 11.0

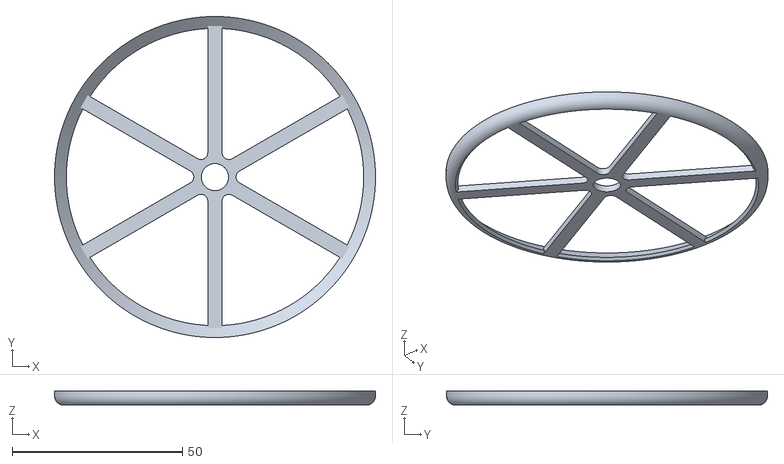
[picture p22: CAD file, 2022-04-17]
STL/Filtration/211 - Filtration, AC Tank Filter Ring.stl
94.4 x 94.4 x 4.26

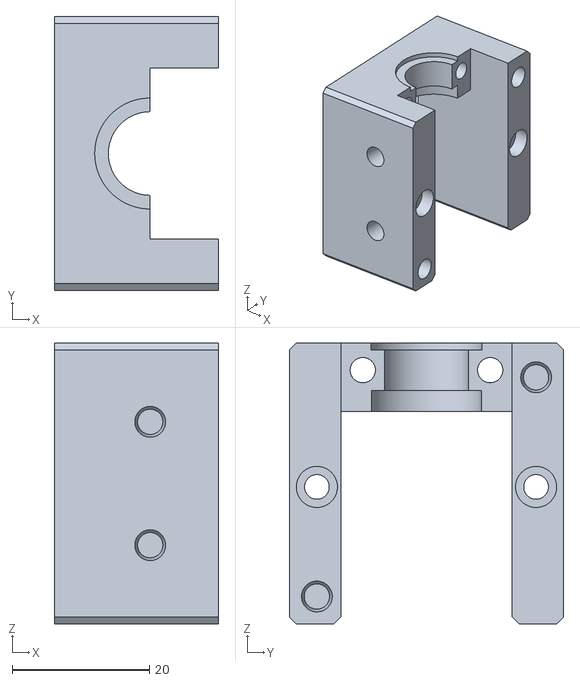
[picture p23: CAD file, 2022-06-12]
STL/040 - Toolhead, Hotend Mounting Bracket.stl
24.0 x 40.0 x 41.0

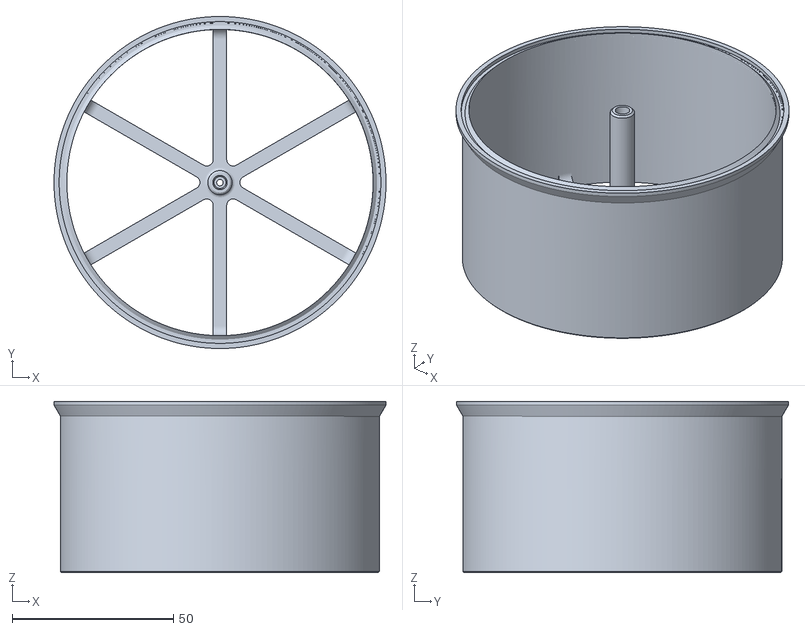
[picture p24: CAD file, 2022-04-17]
STL/Filtration/212 - Filtration, AC Tank, 50mm.stl
103.0 x 103.0 x 53.2

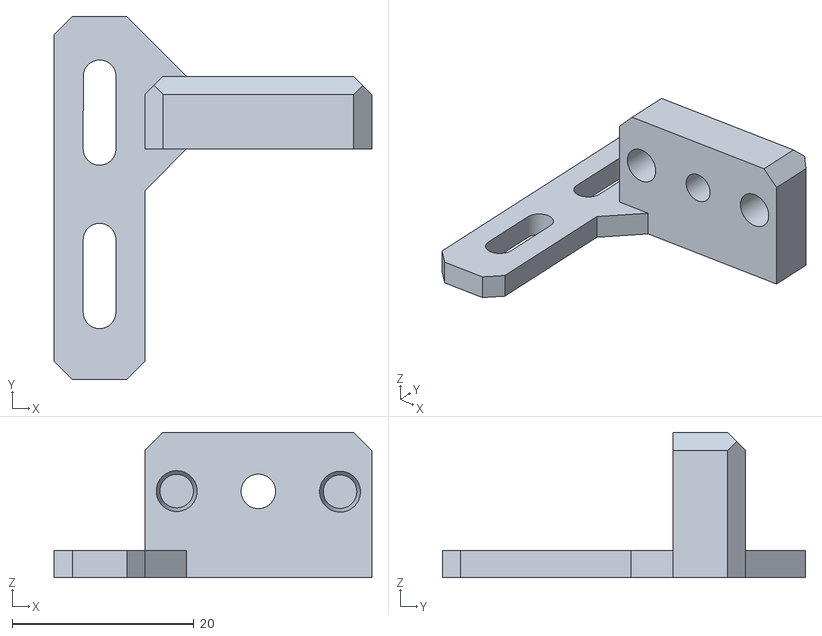
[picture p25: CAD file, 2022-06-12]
STL/051 - Toolhead, BLTouch Mount.stl
35.0 x 40.0 x 16.0

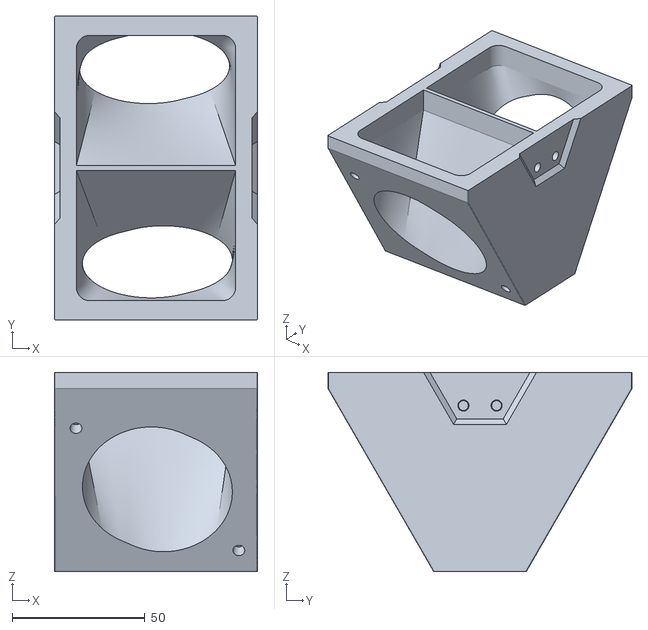
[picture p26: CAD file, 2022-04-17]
STL/Filtration/202 - Filtration, Fan Intake Duct.stl
76.5 x 114.5 x 75.0

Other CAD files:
STL/042 - Toolhead, Cooling Fan Intake.stl
STL/Filtration/204 - Filtration, HEPA Intake Duct.stl
STL/044 - Toolhead, EVA Fan Duct.stl
STL/Filtration/205 - Filtration, HEPA Latch, TPU.stl
CAD/Templates/75mm Fan Exhaust Adapter (TPU).f3d
CAD/Templates/Electrical T Slot Extension.f3d
CAD/Templates/LED Guide Channel.f3d
CAD/Tools/M3 Heat Set Insert Practice Block.f3d
CAD/Tools/M3 Het Set Insert Parameter Block.f3d
STL/001 - XY Pulleys, L Bottom.stl
STL/002 - XY Pulleys, L Top.stl
STL/003 - XY Pulleys, R Bottom.stl
STL/004 - XY Pulleys, R Top.stl
STL/005 - XY Joint, L Top.stl
STL/006 - XY Joint, L Mid.stl
STL/007 - XY Joint, L Bottom.stl
STL/008 - XY Joint, R Top.stl
STL/009 - XY Joint, R Mid.stl
STL/010 - XY Joint, R Bottom.stl
STL/011 - XY Tensioner, Bolt Receiver.stl
STL/012 - XY Tensioner, Idler Seat.stl
STL/013 - XY Tensioner, Tensioner Cap.stl
STL/014 - XY Tensioner, Guide Frame.stl
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

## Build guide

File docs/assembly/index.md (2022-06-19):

---
title: Assembly Guide Introduction
summary: Introduction page to the assembly process.
authors: Jon Harper
date: 2022-04-06
---

*This document is actively being refined and edited for mistaeks.*

Assembly involves a large number of individual parts. We'll do our best to divide the process up into manageable chunks.

For the purposes of this guide, instructions are for an unmodified version of the Clock 3 prototype.

!!! warning
    We will be working with electricity and carefully positioning parts. Patience and caution are needed.

    Rushing any part of assembly now can cause issues later *or even be hazardous*. Take your time, take breaks, and double-check your work!

## Conventions

Like with the [categorization](../bom/index.md#categorization) of parts in the Bill of Materials, there are other conventions we use during the assembly process to identify parts and orient them quickly. We will introduce them as we go through the Preparation section of this Guide.

## Outside Guides and Documentation Links

At various points during assembly and configuration, guides for certain tasks are already available from the manufacturer, developer, or maintainer (or simply a third party). We will often link to an external guide for more detailed explanations of some procedures.

An example of this is in the initial configuration of [MainsailOS](https://github.com/mainsail-crew/MainsailOS). The developers of Mainsail will always have more current documentation regarding installation and setup than ours, so we defer to them where needed.

## A Guided Tour

Below are the stages of the assembly process. Bear in mind that not all steps take the same amount of time.

### Preparation

In a sense, we need to setup a construction site.

- We need to figure out where to put our tools and supplies.
- Double-check our inventory of parts.
- Do some early work and prepare for the rest of the assembly.

### Framing Building Blocks

The frame comes together in sections. The focus is a rigid assembly with squared corners.
### Kinematics

This is a four step process. Essentially, we start with the Z steppers and build up.

1. Z Axis
2. XY Axes
3. X Gantry
4. Belts

### Electronics, Part 1

Before we begin wiring, everything that needs a connector should be in place. This is where we unbox the control board, hotend, and install the rest of the steppers.

### Wiring

In this section, we cover assembling the wiring looms and labeling them. We leave finishing the cabling with connectors for the next section.

### Electronics, Part 2

At this point, it's time to make connectors and actually run our finished cabling. We start from the MCU and work our way up.

### Finishing Up and Closing Up

The is the last of the hardware setup, where we install the door, side panels, and air filtration. We'll check for a solid seal in the chamber and resolve any issues.

Okay, let's check and make sure we have what we need.

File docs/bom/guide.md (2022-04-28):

---
title: Decision Guide
summary: A guide for deciding on variations of the stock Clock 3 printer.
authors: Jon Harper
date: 2022-04-05
---

*This document is actively being refined and edited for mistaeks.*

Clock 3 is still a prototype, so a wide variety of possible configurations have not yet been tested. There is still room for flexibility, however.

## Hotend

The initial prototype is being tested with two hotends: an E3D V6 and a "Haldis Red Lizard" (Phaetus Dragonfly clone). Any V6-compatible hotend with the same heatsink height should work, as long as the width of the heatsink fits within the mount.

## Direct Drive (v. Bowden)

Direct drive with a BMG extruder is currently the only supported configuration. Adding a Bowden configuration is planned, as are other extruders. This section is a placeholder until then.

## Door and Frame

### Door Assembly

MISUMI sells [complete door kits](https://us.misumi-ec.com/vona2/detail/110302284740/). We take a modular approach and buy the parts individually, but some may find a kit appealing. Note that one can purchase this door kit with or without an interior panel. These kits are composed of the following part numbers:

| Part Number | Description | MISUMI PN |
|---|---|---|
| PN553 | Screw, M5-0.8 x 16mm SHCS | SCB5-16 |
| PN710 | Corner Bracket, Door Frame | HBLTC5 |
| PN713 | 2020 Door Panel Gasket, 564mm | HFSSK3-2000 |
| PN714 | 2020 Door Panel Gasket, 646mm | HFSSK3-2000 |
| PN751 | 2020 Door Extrusion, 564mm | HFTF5-2020-564-TPW |
| PN752 | 2020 Door Extrusion, 646mm | HFTF5-2020-646-TPW |
| PN760 | Acrylic Sheet, 577x659x3mm | (included in kit only) |

!!! note
    If you buy the interior panel from MISUMI instead of locally sourcing, shipping costs increase. Adding a panel to a kit only increases the price a few dollars but *may* increase shipping costs more.

Additionally, a 90mm handle ships with the kit. It is not very comfortable and the screw holes are wrong for the outer panel; use the printed handle instead.

If you have M5x16 SHCS on hand already and are having both panels made separately, buying the rest of the parts individually is more cost-effective.

### Windows

#### Acrylic

We use 3mm acrylic. If using 5mm **inner** window panels, change `HFSSK3-2000` to [`HFSSK5-2000`](https://us.misumi-ec.com/vona2/detail/110302375310/?ProductCode=HFSSK5-2000) when sourcing for the door panel gasket.

It is possible to use a 5mm **outer** window panel, but this will require changes to the gasketing behind the door.

!!! note
    At present, we know of no other supplier than MISUMI for this panel mounting gasket. Please notify us if another supplier is found.

#### Polycarbonate (PC)

Switching to PC for the inner panel is a more expensive option. There is no issue with using PC, nor are adjustments required. This can be done relatively affordably for the inner panel by buying a kit.

### Wooden Panels

These will need to be locally fabricated. The wooden panels are 6mm and 12mm thick; approximately the same values in SAE plywood measurements will work with some adjustment. 

- 12mm panels: 15/32" is preferable 
- 6mm panels: Should be thicker, if possible 5/16".

### Insulation

Polyisocyanurate foam is an excellent insulator with superior qualities to polystyrene (Styrofoam) and comparable price. The default thickness all around is 1/2", but this can be increased as desired to better control chamber temperatures.

- Top insulation: up to 1" thick.
- Floor insulation: up to 3/4" thick (will need to be tested).
- Side insulation: up to 1" thick.
- Rear insulation: up to 3/4" thick; additional can be added with some adjustments.

## Electrical

There are an incredible number of different approaches to wiring. While lever nuts can be used, we prefer a connector-based approach for robustness and space considerations. Where possible, any changes to wiring will only impact the Materials list and wiring panel mounts. The panel mounts only connect parts above the flooring, so using lever nuts solely for undercarriage connections is very easily doable.

### Lever Nuts

The front-to-back Z crossbars are ideal mounting positions for lever nuts. In the future, a part holder for this purpose may be added; for now, you can find lots of examples on CAD and STL sharing sites.

### Cable Raceways/Wire Channels

These have not been tested. Mounting the raceways might require additional parts beyond the raceways themselves.

### Ribbon Cables

This is currently being tested and checked for quality sources of silicone ribbon cable, particularly brands that are marked in pairs or rainbow.

### Multi-core Cables

These technically should work but are costly (particularly IGUS's 10+ core cables). Bundling in shielded multi-core cables may be particularly helpful for signal wires, e.g. ABL and endstops, as an alternative to twisting wires.

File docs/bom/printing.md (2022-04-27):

---
title: Printed Parts
summary: Print settings and other information for printed parts.
authors: Jon Harper
date: 2022-04-07
---

*This document is actively being refined and edited for mistaeks.*

!!! note
    Which parts use primary and secondary colors have not been firmly set. This page will later contain information on this, as well.

## 1. Print Settings

### ABS

| Setting | Value | Notes |
|---|---|---|
| Layer Height | 0.24mm  | | 
| Initial Layer Height  | 0.2mm | |
| Layer Width | 0.4mm | |
| Surface Layers | 5 | |
| Perimeters/Walls | 5 (2mm) | |
| Infill | > 25% | Non-structural parts can be printed at 20%  |
| Supports | No | |

### TPU

| Setting | Value | Notes |
|---|---|---|
| Layer Height | 0.2mm | | 
| Initial Layer Height  | 0.2mm | |
| Layer Width | 0.4mm | |
| Surface Layers | 5 | |
| Perimeters/Walls | 4 (1.6mm) | Print feet at 6/2.4mm |
| Infill | 25% | Print feet at 35% or higher |
| Supports | Yes | |

## 2. Parts and Quantity

You can find the [STL Files here](https://github.com/jon-harper/clock-3/tree/main/STL). The number of each part to print is specified in the [Bill of Materials](../bom/bill_of_materials.md), along with a direct link.

## 3. Heat Set Inserts

Many of the parts for Clock 3 require heated inserts. Once you see these in action with ABS, a whole world of possibilities opens. We have two suggestions:

1. Get a heat set insert press or make one ([ex. 1](https://www.thingiverse.com/thing:3613621), [ex. 2](https://hackaday.com/2020/09/09/building-an-affordable-press-for-heat-set-inserts/)). It's an investment. Trust us.
2. Practice ahead of time on the [practice block](https://github.com/jon-harper/clock-3/blob/main/STL/Tools/M3%20Heat%20Set%20Insert%20Practice%20Block.stl). It will use a few inserts, but you'll feel more comfortable working on the printed parts.

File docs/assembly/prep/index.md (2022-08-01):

---
title: Getting Started
summary: Some suggestions for organizing parts for ease.
authors: Jon Harper
date: 2022-04-06
---

Making assembly smooth and logical is important to us. The information here will both help you understand the rest of the guide and offer a few tips, as well.

## 1. Frame Pieces

Pieces of frame of the same length have part numbers, but individual pieces also have an ID. These help locate where on the frame a piece goes and when inserting roll-in tee nuts.

It's important to label each piece so that once we start inserting tee nuts, we don't get the pieces confused. To preserve our own sanity during development, we started labeling frame pieces in the same place, using the **FTL** rule:

- **F**ront
- **T**op
- **L**eft

Every frame piece is labeled with its ID in the front, top left corner *of where it belongs on the printer*. If the front is a cut face on the extrusion, we put a label on the top, in the front left corner instead. This is a consistent strategy we use throughout this assembly guide.

[Here's an example](../img/A1.jpg) of a labeled part and how the FTL scheme works in practice. This picture is of frame piece `A1`, which is stickered in the upper left. With this as a reference, we can show each face of the extrusion and where the tee nuts belong.

We will label each piece before we get started assembling the frame. For the moment, keep them organized by length/part number.

## 2. Printed Part Numbers

Most printed parts have their part number embossed somewhere. Once installed the number won't be visible--they are solely there to help you find the part you are looking for. Anything without a part number is labeled in the notes column of the Bill of Materials. We recommend putting these unnumbered parts in bags and labeling them.

!!! note
    Parts are also labeled with an 'L' or 'R' if there are two parts that are mirrors.

## 3. The Later Area

There are some things you won't need until near the very end of assembly. We can set these parts in "Later Area" to keep what you don't need immediately stored. Here's the list:

| ID | Description |
|---|---|
| PN9XX | The entire Electrical section of the BOM. |
| PN8XX | The entire Misc. section of the BOM. |
| PN797 | Foam Weatherstripping |
| PN4XX | The entire Toolhead section of the BOM. |
| MN001 | Activated Carbon |
| MN2XX | All electrical connectors |

Once we have the frame and some other bits together, we'll gather more parts.

## 4. Extra Tips

There are quite a few parts we'll only need one of, or will only need at certain times. On the other hand, we need screws for pretty much everything. 

- Organizing your parts by category and purpose will quickly locate parts.
- Placing small parts in bags with their part number also helps.
- Keep a small box close with just the brackets, screws, and other fasteners.
- Leave electronics in their packaging until needed. They tend to go straight from box to some form of mount.

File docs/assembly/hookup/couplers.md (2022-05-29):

---
title: Finishing Out the Enclosure
summary: Final parts to install in the enclosure before wiring begins.
authors: Jon Harper
date: 2022-05-23
---

*This document is a placeholder until more content is generated.*

## 1. Exhaust Coupler

### A. Parts

| ID | Qty | Description |
|---|-----|---|
| PN121 | 1 | Frame, Exhaust Coupler |
| PN532 | 2 | Screw, M5-0.8 x 12mm BHCS |
| PN574 | 2 | Tee Nut, 6mm Slot, M5, Drop In |

### B. Steps

| Step | Example |
|---|---|

## 2. Exterior PTFE Coupler

### A. Parts

| ID | Qty | Description |
|---|-----|---|
| PN120 | 1 | Frame, PTFE Coupler |
| PN122 | 1 | Frame, PTFE Coupling Guide, TPU |
| PN532 | 2 | Screw, M5-0.8 x 12mm BHCS |
| PN574 | 2 | Tee Nut, 6mm Slot, M5, Drop In |
| PN821 | 2 | Coupler, Pneumatic, PC4-M10 |

### B. Steps

| Step | Example |
|---|---|
| 

## 3. Rear PTFE Guide

### A. Parts

| ID | Qty | Description |
|---|-----|---|
| PN100 | 1 | Misc, Rear PTFE Tube Guide |
| PN532 | 1 | Screw, M5-0.8 x 12mm BHCS |
| PN577 | 1 | Washer, M5, Split Lock |

### B. Steps

| Step | Example |
|---|---|
| 

## 4. Camera

### A. Parts

| ID | Qty | Description |
|---|-----|---|
| PN087 | 1 | Electrical, Camera Mount |
| PN088 | 1 | Electrical, Camera Stand |
| PN500 | 1 | Screw, M3-0.5 x 6mm SHCS |
| PN532 | 2 | Screw, M5-0.8 x 12mm BHCS |
| PN577 | 2 | Washer, M5, Split Lock |
| PN985 | 1 | Raspberry Pi Camera |

### B. Steps

| Step | Example |
|---|---|
| 

## 5. Grounding Wire

### A. Parts

| ID | Qty | Description |
|---|-----|---|
| PN578 | 1 | Washer, M5 x 10mm |
| PN530 | 1 | Screw, M5-0.8 x 8mm BHCS |

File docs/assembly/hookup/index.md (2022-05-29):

---
title: Connections Overview
summary: An overview of running cabling during assembly.
authors: Jon Harper
date: 2022-04-11
---

*This document is a placeholder until more content is generated.*

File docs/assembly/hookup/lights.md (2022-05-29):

---
title: Light Installation
summary: Instructions for RGB LED ligth installation.
authors: Jon Harper
date: 2022-05-28
---

*This document is a placeholder until more content is generated.*

## 1. Preparing the Strips

### A. Parts

| ID | Qty | Description |
|---|-----|---|
| PN082 | 3 | Lighting, LED Guide, 12mm |
| PN970 | 36  | 5050 RGB LED Pixel, 12mm PCB, 16.6mm Pitch |

### B. Steps

| Step | Example |
|---|---|

## 2. Installation

### A. Parts

| ID | Qty | Description |
|---|-----|---|
| PN500 | 6 | Screw, M3-0.5 x 6mm SHCS |
| PN573 | 6 | Tee Nut, 6mm Slot, M3, Drop In |

### B. Steps

| Step | Example |
|---|---|
|

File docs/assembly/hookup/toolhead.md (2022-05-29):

---
title: Finishing Out the Toolhead
summary: Final parts to install on the toolhead.
authors: Jon Harper
date: 2022-05-28
---

*This document is a placeholder until more content is generated.*

## 1. Part Fan

### A. Parts

| ID | Qty | Description |
|---|-----|---|
| PN504 | 2 | Screw, M3-0.5 x 20mm, SHCS |
| PN951 | 1 | Fan, Radial, 50mm x 15mm, 12/24V |

### B. Steps

| Step | Example |
|---|---|

## 2. Hotend Cooling Fan

### A. Parts

| ID | Qty | Description |
|---|-----|---|
| PN504 | 2 | Screw, M3-0.5 x 20mm, SHCS |
| PN506 | 2 | Screw, M3-0.5 x 30mm, SHCS |
| PN950 | 1 | Fan, Axial, 40mm x 20mm, 12/24V |

### B. Steps

| Step | Example |
|---|---|
| 

## 3. BLTouch

### A. Parts

| ID | Qty | Description |
|---|-----|---|
| PN051 | 1 | Toolhead, BLTouch Mount |
| PN485 | 1 | BLTouch V3.1 |
| PN500 | 2 | Screw, M3-0.5 x 6mm SHCS |
| PN501 | 1 | Screw, M3-0.5 x 8mm SHCS |
| PN503 | 1 | Screw, M3-0.5 x 16mm SHCS |

### B. Steps

| Step | Example |
|---|---|
| 

## 4. Hotend Heat Block

### A. Parts

| ID | Qty | Description |
|---|-----|---|
| PN971 | 1 | Thermistor, NTC 100K, E3D V6 cartridge |
| PN972 | 1 | Heater Cartridge, 24V |

### B. Steps

| Step | Example |
|---|---|
|

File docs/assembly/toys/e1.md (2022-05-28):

---
title: First Extrusion
summary: Preparation instructions for the E1 electronics extrusion.
authors: Jon Harper
date: 2022-04-11
---

*This document is a placeholder until more content is generated.*

## 1. Prepare Extrusion

### A. Parts

| ID | Qty | Description |
|---|-----|---|
| E1 | 1 | 2020 Extrusion, 620mm |
| PN551 | 8\* | Screw, M4-0.7 x 6mm Set Screw |
| PN701 | 4 | Corner Bracket, Inside Hidden |

\* These are usually sold with the corner brackets.

### B. Steps

| Step | Example |
|---|---|

## 2. Add CPU and MCU Brackets

### A. Parts

| ID | Qty | Description |
|---|-----|---|
| PN076 | 1 | Electrical, L Octopus Board Mount |
| PN077 | 1 | Electrical, R Octopus Board Mount |
| PN083 | 1 | Electrical, L RPi Board Mount |
| PN084 | 1 | Electrical, L RPi Board Mount |
| PN532 | 4 | Screw, M5-0.8 x 12mm BHCS |
| PN577 | 4 | Washer, M5, Split Lock |

### B. Steps

| Step | Example |
|---|---|

## 3. Install MCU

### A. Parts

| ID | Qty | Description |
|---|-----|---|
| PN500 | 4 | Screw, M3-0.5 x 6mm SHCS |
| PN980 | 1 | BIGTREETECH Octopus V1.1 |
| PN981 | 5 | Stepper Driver, TMC2209 |

### B. Steps

| Step | Example |
|---|---|

## 4. Install CPU

### A. Parts

| ID | Qty | Description |
|---|-----|---|
| PN500 | 4 | Screw, M3-0.5 x 6mm SHCS |
| PN802 | 1 | Heatsink, 14x14x6 |
| PN984 | 1 | Raspberry Pi 4 Model B 2GB |
| PN965 | 1 | Micro HDMI to HDMI Adapter |

### B. Steps

| Step | Example |
|---|---|

## 5. (Optional) Install Raspberry Pi Buck Converter

### A. Parts

| ID | Qty | Description |
|---|-----|---|
| PN501 | 2 | Screw, M3-0.5 x 8mm SHCS |
| PN573 | 2 | Tee Nut, 6mm Slot, M3, Drop In |
| PN987 | 1 | Buck Converter, 3A, USB C out |

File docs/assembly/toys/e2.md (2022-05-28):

---
title: Second Extrusion
summary: Preparation instructions for the E2 electronics extrusion.
authors: Jon Harper
date: 2022-04-11
---

*This document is a placeholder until more content is generated.*

## 1. Prepare Extrusion

### A. Parts

| ID | Qty | Description |
|---|-----|---|
| E2 | 1 | 2020 Extrusion, 620mm |
| PN551 | 8 | Screw, M4-0.7 x 6mm Set Screw |
| PN701 | 4 | Corner Bracket, Inside Hidden |

### B. Steps

| Step | Example |
|---|---|

## 2. Install SP901E

### A. Parts

| ID | Qty | Description |
|---|-----|---|
| PN530 | 2 | Screw, M5-0.8 x 8mm BHCS |
| PN578 | 2 | Washer, M5x10mm |
| PN986 | 1 | Signal Amplifier, SP901E |

### B. Steps

| Step | Example |
|---|---|

## 3. Install PSU

### A. Parts

| ID | Qty | Description |
|---|-----|---|
| PN086 | 2 | Electrical, PSU Mount |
| PN532 | 2 | Screw, M5-0.8 x 12mm BHCS |
| PN557 | 4 | Screw, M4-0.7 x 8mm BHCS |
| PN577 | 2 | Washer, M5, Split Lock |
| PN912 | 1 | Power Supply, 24V, 450W |

### B. Steps

| Step | Example |
|---|---|

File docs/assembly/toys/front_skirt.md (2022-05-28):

---
title: Front Skirt
summary: Installation instructions for the front skirt panels.
authors: Jon Harper
date: 2022-05-27
---

*This document is a placeholder until more content is generated.*

## 1. Prepare Right Front End

### A. Parts

| ID | Qty | Description |
|---|-----|---|
| PN105 | 1 | Skirt, R Front End |
| PN911 | 1 | Switch, Panel Mount, >5A VAC |

### B. Steps

| Step | Example |
|---|---|

## 2. Prepare Left Front End

### A. Parts

| ID | Qty | Description |
|---|-----|---|
| PN104 | 1 | Skirt, L Front End |
| PN501 | 8 | Screw, M3-0.5 x 8mm SHCS |
| PN961 | 1 | Panel Mount Extension, RJ-45 |
| PN960 | 2 | Panel Mount Extension, USB Type A |
| PN962 | 1 | Panel Mount Extension, HDMI |

### B. Steps

| Step | Example |
|---|---|

## 3. Prepare Display Slot

### A. Parts

| ID | Qty | Description |
|---|-----|---|
| PN110 | 1 | Skirt, SD Card Reader Mount |
| PN112 | 1 | Skirt, Display Mount |
| PN113 | 1 | Skirt, Display Slot |
| PN500 | 6 | Screw, M3-0.5 x 6mm SHCS |
| PN501 | 3 | Screw, M3-0.5 x 8mm SHCS |
| PN963 | 1 | Micro SD to SD Extension |
| PN982 | 1 | Mini 12864 LCD |

### B. Steps

| Step | Example |
|---|---|

## 4. Prepare Fans

### A. Parts

| ID | Qty | Description |
|---|-----|---|
| PN102 | 2 | Skirt, 80mm Fan Mount |
| PN103 | 2 | Skirt, 80mm Fan Exterior Grill |
| PN111 | 2 | Skirt, 80mm Fan Finger Guard |
| PN507 | 8 | Screw, M3-0.5 x 35mm SCHS |
| PN952 | 2 | Fan, Axial, 80mm x 25mm |

### B. Steps

| Step | Example |
|---|---|

## 5. Connect Skirt Panels

### A. Parts

| ID | Qty | Description |
|---|-----|---|
| PN104 | 1 | Skirt, L Front End |
| PN105 | 1 | Skirt, R Front End |
| PN108 | 1 | Skirt, Hexagon Grill |
| PN501 | 10  | Screw, M3-0.5 x 8mm SHCS |

You will also need the display slot assembly and two fan slot assemblies.

### B. Steps

| Step | Example |
|---|---|

## 6. Install Panels

### A. Parts

| ID | Qty | Description |
|---|-----|---|
| PN530 | 2 | Screw, M5-0.8 x 8mm BHCS |
| PN532 | 4 | Screw, M5-0.8 x 12mm BHCS |
| PN577 | 4 | Washer, M5, Split Lock |
| PN824 | 1 | SD Card |

### B. Steps

| Step | Example |
|---|---|

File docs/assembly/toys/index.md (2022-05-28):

---
title: Initial Electronics Overview
summary: Introduction to assembling the X gantry and electronics.
authors: Jon Harper
date: 2022-04-11
---

*This document is a placeholder until more content is generated.*

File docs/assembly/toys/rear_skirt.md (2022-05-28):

---
title: Rear Skirt
summary: Installation instructions for the rear skirt panels.
authors: Jon Harper
date: 2022-05-27
---

*This document is a placeholder until more content is generated.*

## 1. Prepare Power Socket Panel

### A. Parts

| ID | Qty | Description |
|---|-----|---|
| PN107 | 1 | Skirt, R Rear End |
| PN501 | 2 | Screw, M3-0.5 x 8mm SHCS |
| PN570 | 2 | Hex Nut, M3 |
| PN913 | 1 | Fuse, 5x20, Glass, Fast Blow, 5A |
| PN964 | 1 | IEC C13 Socket with Fuse Holder |

### B. Steps

| Step | Example |
|---|---|

## 2. Connect Skirt Panels

### A. Parts

| ID | Qty | Description |
|---|-----|---|
| PN106 | 1 | Skirt, L Rear End |
| PN107 | 1 | Skirt, R Rear End |
| PN108 | 4 | Skirt, Hexagon Grill |
| PN501 | 10  | Screw, M3-0.5 x 8mm SHCS |

### B. Steps

| Step | Example |
|---|---|

## 3. Install Panels

### A. Parts

| ID | Qty | Description |
|---|-----|---|
| PN530 | 2 | Screw, M5-0.8 x 8mm BHCS |
| PN532 | 5 | Screw, M5-0.8 x 12mm BHCS |
| PN577 | 5 | Washer, M5, Split Lock |

### B. Steps

| Step | Example |
|---|---|

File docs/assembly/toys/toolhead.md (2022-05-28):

---
title: Toolhead Setup
summary: Pre-wiring installation of toolhead components.
authors: Jon Harper
date: 2022-04-11
---

*This document is a placeholder until more content is generated.*

## 1. Part Cooling Duct

### A. Parts

| ID | Qty | Description |
|---|-----|---|
| PN044 | 1 | Toolhead, EVA Fan Duct |
| PN045 | 1 | Toolhead, Part Fan Mount |
| PN500 | 2 | Screw, M3-0.5 x 6mm SHCS |
| PN504 | 2 | Screw, M3-0.5 x 20mm, SHCS |

### B. Steps

| Step | Example |
|---|---|

## 2. Hotend

### A. Parts

| ID | Qty | Description |
|---|-----|---|
| PN040 | 1 | Toolhead, Hotend Mounting Bracket |
| PN041 | 1 | Toolhead, Hotend Locking Collar |
| PN400 | 1 | E3D V6 Hotend\* |
| PN505 | 2 | Screw, M3-0.5 x 25mm SHCS |
| PN506 | 2 | Screw, M3-0.5 x 30mm SHCS |

\* Or compatible. In this example we are using a "Haldis Red Lizard".

### B. Steps

| Step | Example |
|---|---|

## 3. Extruder

### A. Parts

| ID | Qty | Description |
|---|-----|---|

### B. Steps

| Step | Example |
|---|---|

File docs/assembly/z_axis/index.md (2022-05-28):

---
title: Z Axis Overview
summary: Introduction to assembling the Z Axis.
authors: Jon Harper
date: 2022-04-11
---

*This document is actively being refined and edited for mistaeks.*

The Z axis is almost entirely symmetrical. There are two Z steppers, each with its own driver and limit switch. The left stepper is Z1, the right is Z2. Making sure those steppers and the linear rails are aligned prevents binding, so we will take some time to ensure both halves are aligned relative to one another during this process.

## Assembly Order

After the bed is assembled, the rest of the assembly process is centered on the linear rails and lead screws:

1. Assemble the bed frame.
2. Install the Z steppers and floor sealing bearing.
3. Install the Z gantries and attach the bed frame.
4. Install the limit switches and align the Z linear rails.
5. Add the bed to the bed frame.
6. Lubricate and install the lead screws.

When you're ready, we'll get started.

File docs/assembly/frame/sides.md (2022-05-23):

---
title: Side Frames
summary: Instructions on assembling left and right sides of the frame.
authors: Jon Harper
date: 2022-04-07
---

*This document is actively being refined and edited for mistaeks.*

## 1. Assembling the Sides

We will start with the left side, but have the parts ready for both.
### A. Parts

| ID | Qty | Description |
|---|-----|---|
| L1 | 1 | 2020 Extrusion, 620mm |
| L2 | 1 | 2040 Extrusion, 620mm |
| L3 | 1 | 2040 Extrusion, 800mm |
| L4 | 1 | 2040 Extrusion, 800mm |
| R1 | 1 | 2020 Extrusion, 620mm |
| R2 | 1 | 2040 Extrusion, 620mm |
| R3 | 1 | 2040 Extrusion, 800mm |
| R4 | 1 | 2040 Extrusion, 800mm |
| PN532 | 16  | Screw, M5-0.8 x 12mm BHCS |
| PN577 | 16  | Washer, M5, Split Lock |
| PN700 | 8 | Corner Bracket, Tapped |

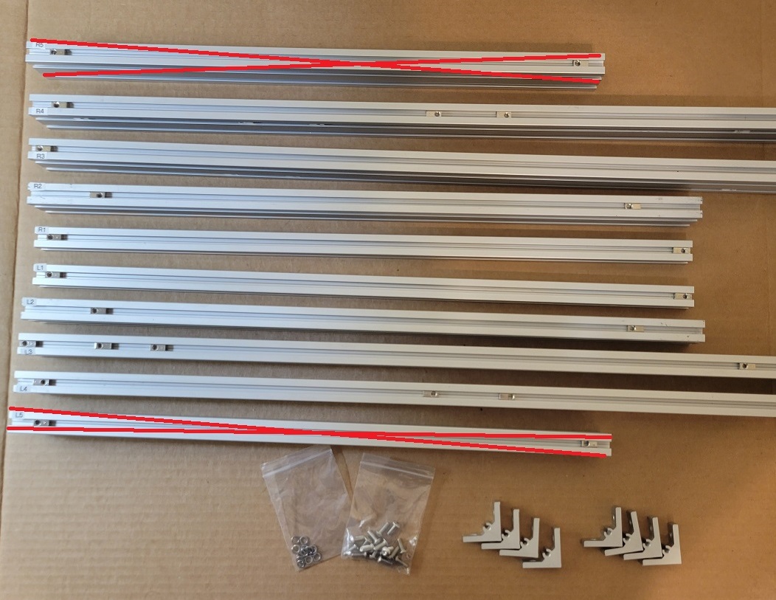
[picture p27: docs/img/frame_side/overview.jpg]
parts overview


!!! note
    L5 and R5 will be added in later in this section.

!!! caution
    Always square each corner before tightening a bracket. See the previous section for instructions.

### B. General Steps

The steps for both sides are the same:

1. Square the first section and attach a bracket.
2. Use two (2) M5x12mm and two (2) split lock washers.
3. Add another section of frame with a bracket and pair of screws and lock washers.
4. Keep going around the corners adding brackets.
5. Continually check your work for a good, square fit as you go.
6. Attach the fourth bracket. If the frame is squared, it will readily slide in place.

### C. Left Side

| Step | Example |
|---|---|
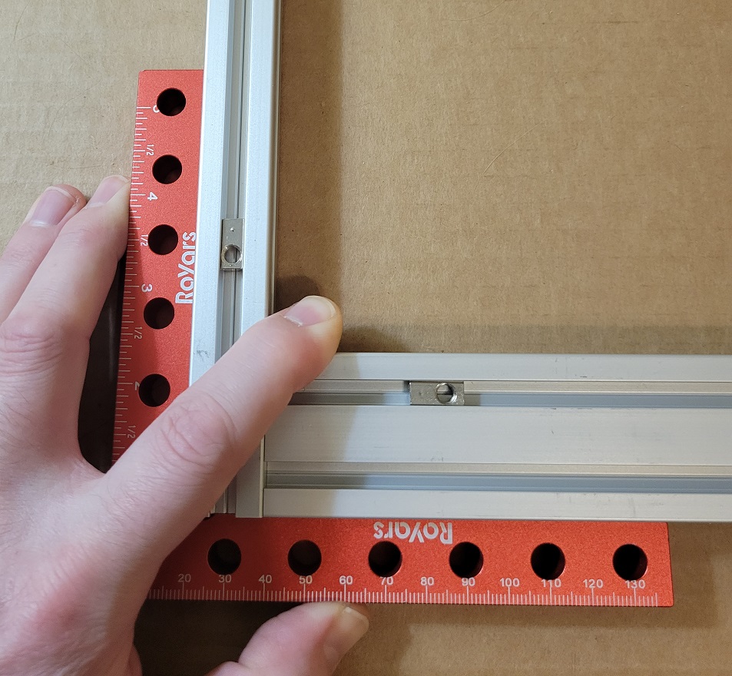
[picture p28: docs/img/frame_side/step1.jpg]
step 1
| Attach L1 and L3 |  |
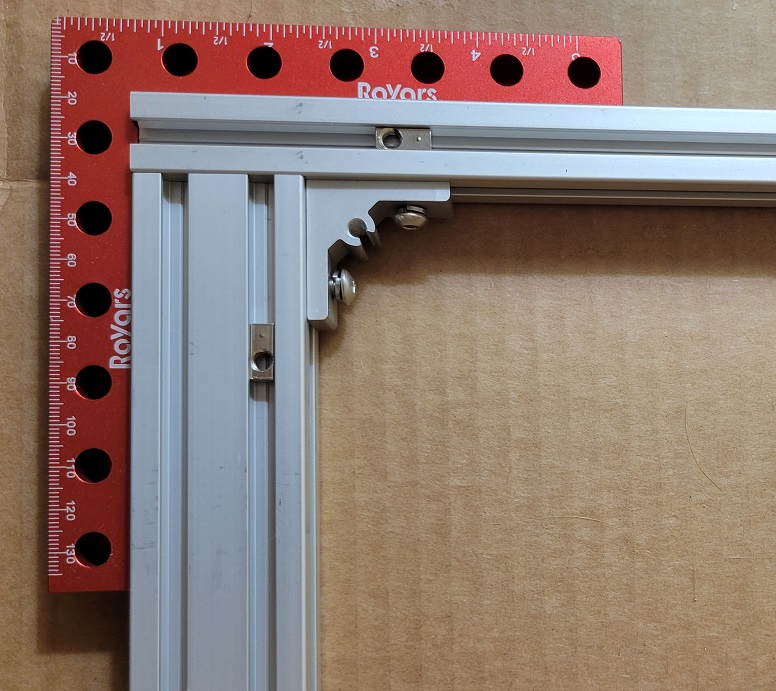
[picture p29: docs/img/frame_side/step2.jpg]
step 2
| Attach L1 and L4 |  |
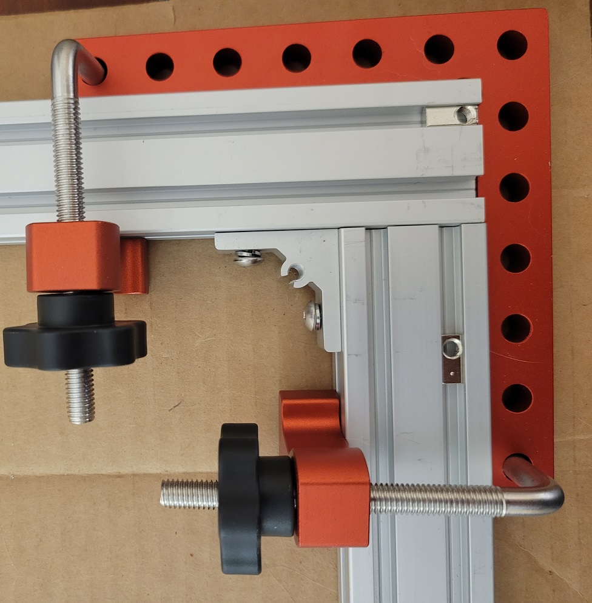
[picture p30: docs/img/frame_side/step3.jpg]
step 3
| Attach L2 and L4 |  |
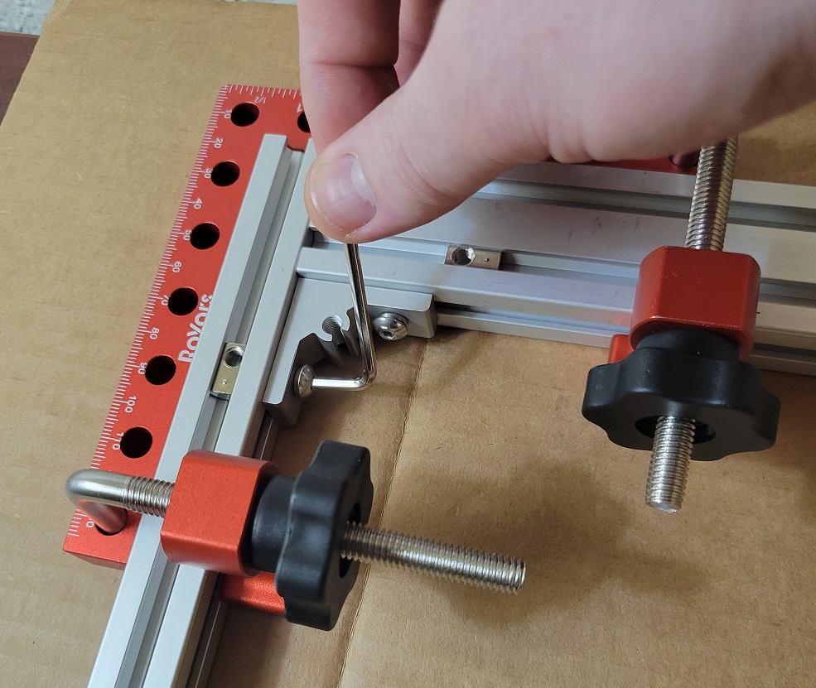
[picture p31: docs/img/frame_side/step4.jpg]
step 4
| Attach L2 and L3 |  |

### D. Right Side

Repeat the above steps with the pieces for the right side (R1-R4) and the remaining fasteners.
## 2. L5 and R5 Crossbars

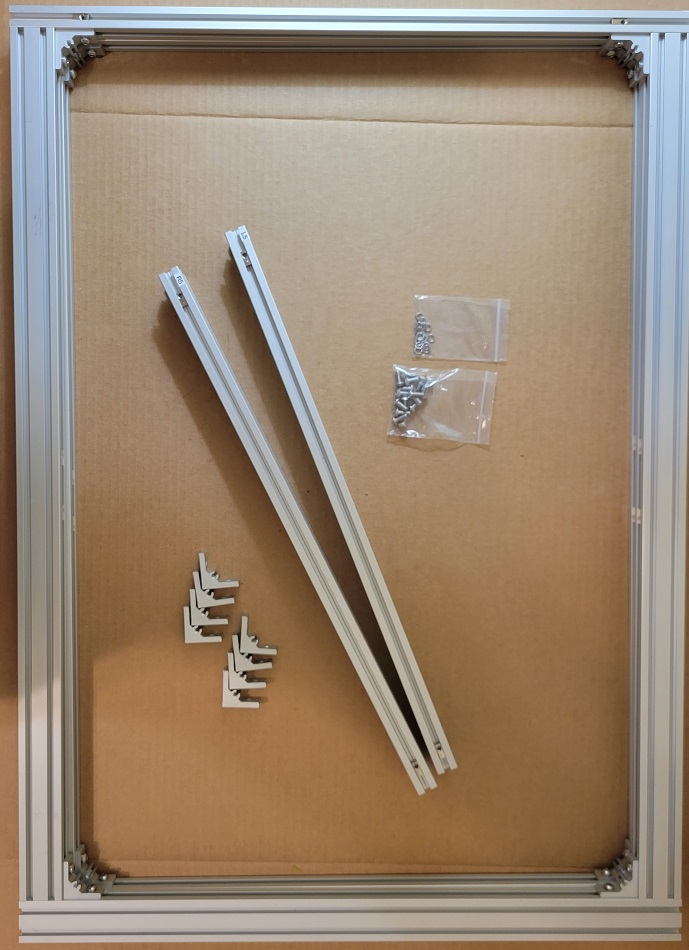
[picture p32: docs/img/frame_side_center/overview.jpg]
overview


### A. Parts

| ID | Qty | Description |
|---|-----|---|
| L5 | 1 | 2020 Extrusion, 540mm |
| R5 | 1 | 2040 Extrusion, 540mm |
| PN532 | 8 | Screw, M5-0.8 x 12mm BHCS |
| PN577 | 8 | Washer, M5, Split Lock |
| PN700 | 4 | Corner Bracket, Tapped |

### B. General Steps

As above, the steps are the same for both sides.

1. Position the crossbars roughly centered on the side frame, or about 400mm from the edge
2. Loosely fasten two (2) brackets into place with M5x12 screws and lock washers.
3. Use a square before tightening the screws.
4. Once the top brackets are tightened, add in the bottom brackets.

!!! note
    You can set the second side of the frame on top of the first to simplify positioning for the second set of brackets.

### C. Left Side

| Step | Example |
|---|---|
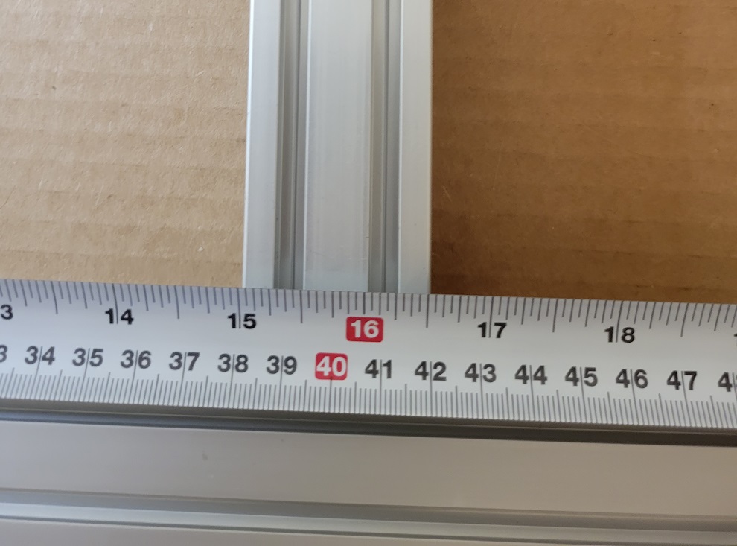
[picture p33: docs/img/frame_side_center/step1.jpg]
step 1
| Measure 400mm from the edge. |  |
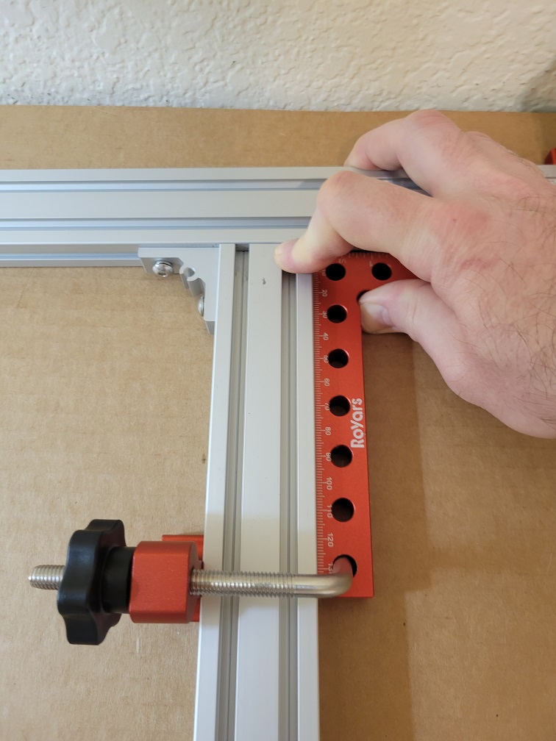
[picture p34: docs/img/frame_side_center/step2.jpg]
step 2
| Install two brackets. |  |
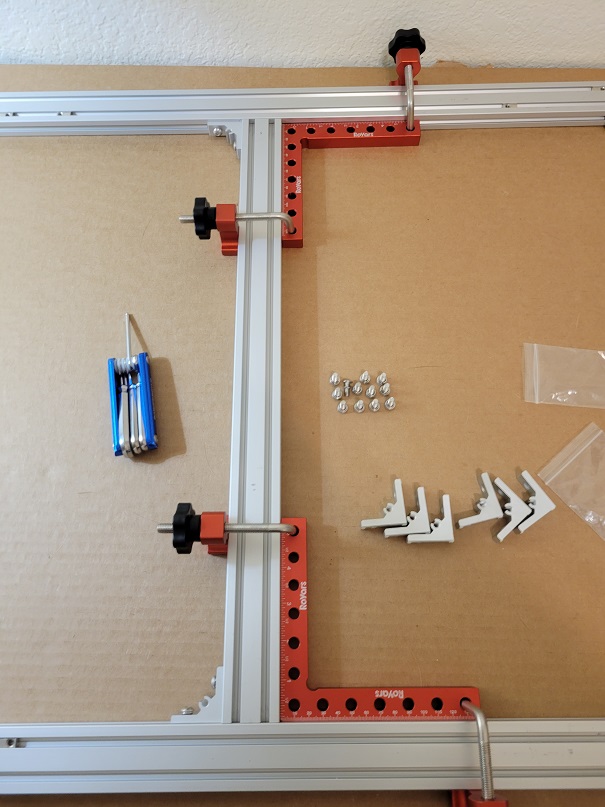
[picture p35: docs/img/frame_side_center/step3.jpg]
step 3
| Square the crosspiece. |  |
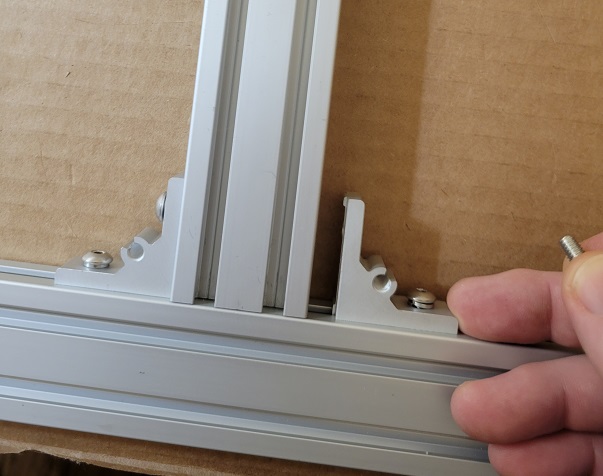
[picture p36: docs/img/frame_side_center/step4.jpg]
step 4
| Add bottom brackets | 

### D. Right Side

Repeat the steps above for the right side with R5 and the remaining fasteners.

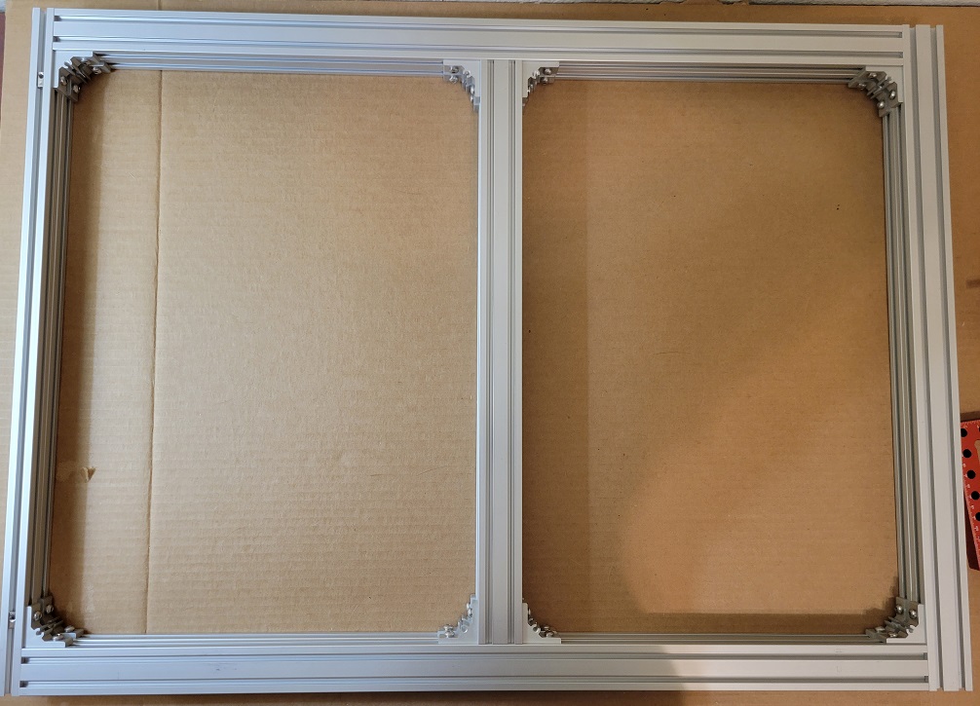
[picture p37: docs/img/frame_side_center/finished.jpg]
finished


## 3. Bracket Covers

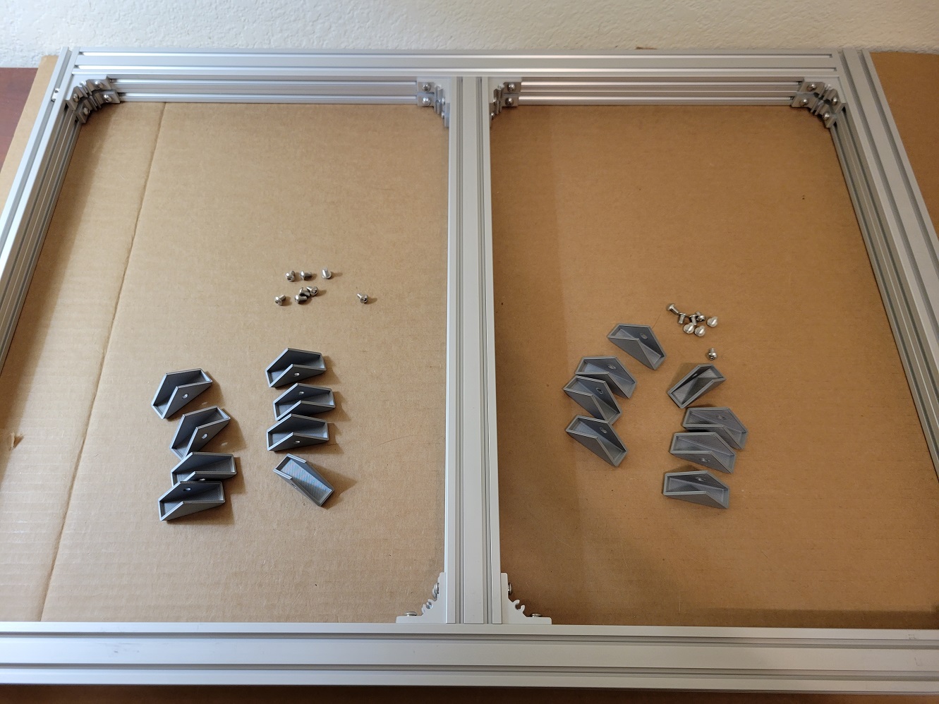
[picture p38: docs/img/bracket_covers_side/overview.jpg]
bracket covers


### A. Parts

| ID | Qty | Description |
|---|-----|---|
| PN090 | 16  | Misc, Corner Bracket Cover |
| PN530 | 16  | Screw, M5-0.8 x 8mm BHCS |

### B. Steps

| Step | Example |
|---|---|
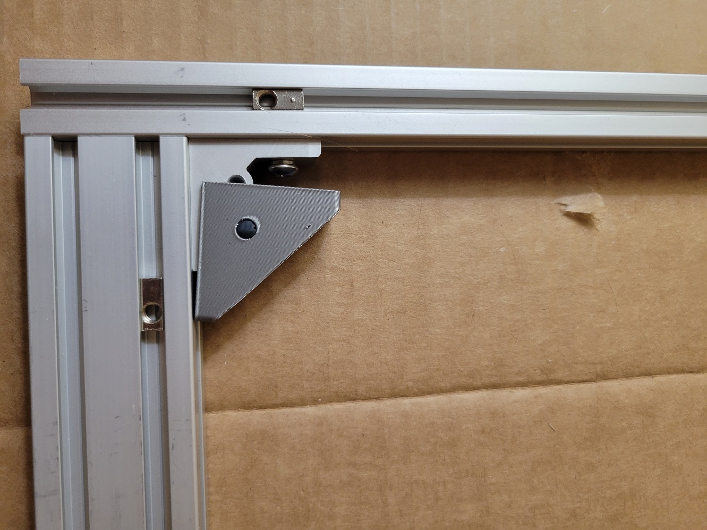
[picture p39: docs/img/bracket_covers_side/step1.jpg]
step 1
| Slip a cover over the bracket. |  |
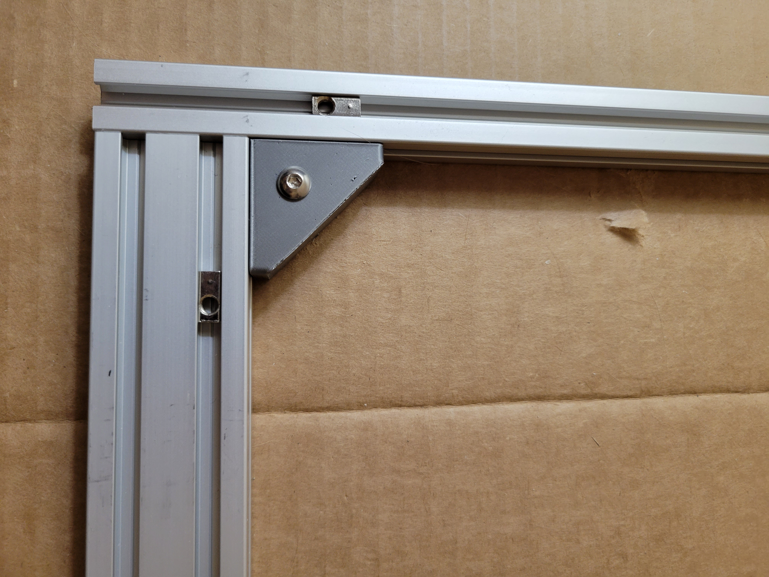
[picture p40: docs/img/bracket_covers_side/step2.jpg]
step 2
| Add an M5x8 screw and tighten. |  |
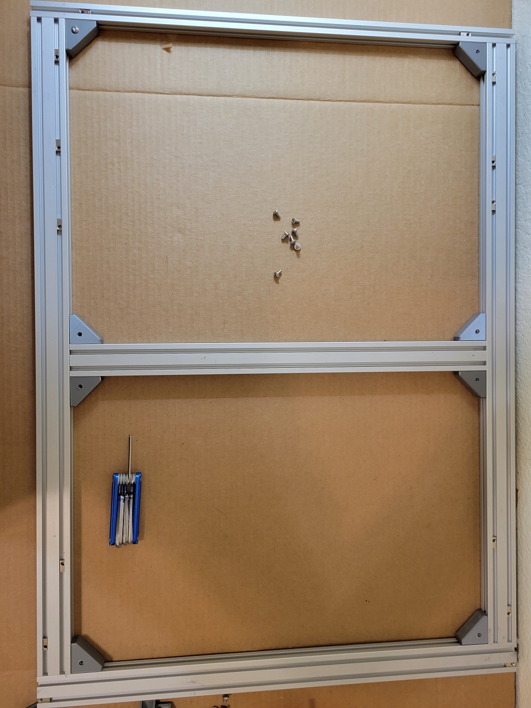
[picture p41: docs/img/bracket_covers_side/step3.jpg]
step 3
| Repeat for the remaining brackets. |  |

## 4. Frame Feet

### A. Parts

| ID | Qty | Description |
|---|-----|---|
| PN092 | 2 | Misc, Printer Base Foot, TPU |
| PN532 | 8 | Screw, M5-0.8 x 12mm BHCS |

### B. Steps

| Step | Example |
|---|---|
| Lay the left side of the frame flat. | |
| Line up the screw holes of one (1) of the Base Feet with the prepared roll-in tee nuts on the underside of L2 | |
| Fasten the foot with two (2) M5 x 12mm screws. | |
| Repeat for the other foot. |
| Install the other two feet on the right side in the same manner. | |

<!-- [![finished](../../img/bracket_covers_side/finished.jpg)](../../img/bracket_covers_side/finished.jpg) -->

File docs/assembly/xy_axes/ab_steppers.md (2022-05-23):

---
title: A and B Steppers
summary: Installation directions for the alpha and beta steppers.
authors: Jon Harper
date: 2022-05-22
---

*This document is a placeholder until more content is generated.*

## 1. Stepper Preparation

### A. Parts

| ID | Qty | Description |
|---|-----|---|
| PN016 | 2 | XY Steppers, Stepper Mount |
| PN500 | 4 | Screw, M3-0.5 x 6mm SHCS |
| PN501 | 4 | Screw, M3-0.5 x 8mm SHCS |
| PN502 | 4\* | Screw, M3-0.5 x 12mm SHCS |
| PN580 | 2 | Coupler, 5mm to 8mm, Rigid |
| PN800 | 2 | Vibration Damper, NEMA 17 |
| PN801 | 2 | Heatsink, 42x42x12mm |
| PN900 | 2 | Stepper, NEMA 17, 48mm, 17HM19-2004S |

\* Included with rigid coupler.

### B. Steps

## 2. Drive Shaft

### A. Parts

| ID | Qty | Description |
|---|-----|---|
| PN095 | 2 | Frame, Bearing Alignment Slider, TPU |
| PN600 | 2 | Ball Bearing, F688ZZ |
| PN611 | 2 | Pulley, 2GT-2, 30T, 8mm Bore |
| PN621 | 2 | Linear Rod, 8mm OD, 250mm |

### B. Steps

## 3. Mounting the Steppers

### A. Parts

| ID | Qty | Description |
|---|-----|---|
| PN015 | 2 | XY Steppers, Vibration Damper, TPU |
| PN535 | 4 | Screw, M5-0.8 x 60mm BHCS |
| PN551 | 2\* | Set Screw, M4-0.7 x 4mm |
| PN577 | 4 | Washer, M5, Split Lock |
| PN582 | 2 | Lock Collar, 8mm |

\* Set screws are usually packaged with the lock collars.

### B. Steps

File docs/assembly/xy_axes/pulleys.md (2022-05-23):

---
title: Stepper Pulley Assembly
summary: Instructions for assembling the XY pulley modules.
authors: Jon Harper
date: 2022-05-22
---

*This document is a placeholder until more content is generated.*

## 1. Pulley Module Bottoms

### A. Parts

| ID | Qty | Description |
|---|-----|---|
| PN001 | 1  | XY Pulleys, L Bottom |
| PN003 | 1  | XY Pulleys, R Bottom |
| PN532 | 4  | Screw, M5-0.8 x 12mm BHCS |
| PN577 | 4  | Washer, M5, Split Lock |
| PN600 | 2  | Bearing, F688ZZ |

### B. Steps

## 2. Idlers

### A. Parts

| ID | Qty | Description |
|---|-----|---|
| PN578 | 4  | Washer, M5x10mm |
| PN601 | 12 | Bearing, F695-2RS |
| PN620 | 4  | Dowel Pin, 5mm OD, 25mm |

### B. Steps

## 3. Pulley Module Tops and Rail Guides

### A. Parts

| ID | Qty | Description |
|---|-----|---|
| PN002 | 1  | XY Pulleys, L Top |
| PN004 | 1  | XY Pulleys, R Top |
| PN017 | 1  | XY Motion, L Y Rail Guide |
| PN018 | 1  | XY Motion, R Y Rail Guide |
| PN091 | 1  | Misc, Limit Switch Cap |
| PN503 | 2  | Screw, M3-0.5 x 16mm SHCS |
| PN506 | 4  | Screw, M3-0.5 x 30mm SHCS |
| PN532 | 2  | Screw, M5-0.8 x 12mm BHCS |
| PN533 | 2  | Screw, M5-0.8 x 16mm BHCS |
| PN536 | 2  | Screw, M5-0.8 x 20mm BHCS |
| PN577 | 6  | Washer, M5, Split Lock |
| PN600 | 2  | Bearing, F688ZZ |
| PN910 | 1  | Limit Switch |

### B. Steps

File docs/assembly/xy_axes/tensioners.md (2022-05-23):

---
title: Tensioners
summary: Installation instructions for the XY belt tensioners.
authors: Jon Harper
date: 2022-05-22
---

*This document is a placeholder until more content is generated.*

## 1. Idler Carriers

### A. Parts

| ID | Qty | Description |
|---|-----|---|
| PN011 | 2 | XY Tensioner, Bolt Receiver |
| PN012 | 2 | XY Tensioner, Idler Seat |
| PN505 | 4 | Screw, M3-0.5 x 25mm SHCS |
| PN572 | 2 | Hex Nut, M5 |
| PN578 | 4 | Washer, M5x10mm |
| PN601 | 4 | Bearing, F695-2RS |
| PN620 | 2 | Dowel Pin, 5mm OD, 25mm |

### B. Steps

## 2. Left Tensioner

### A. Parts

| ID | Qty | Description |
|---|-----|---|
| PN013 | 1 | XY Tensioner, Tensioner Cap |
| PN014 | 1 | XY Tensioner, Guide Frame |
| PN508 | 3 | Screw, M3-0.5 x 40mm SHCS |
| PN532 | 2 | Screw, M5-0.8 x 12mm BHCS |
| PN534 | 3 | Screw, M5-0.8 x 25mm BHCS |
| PN577 | 4 | Washer, M5, Split Lock |

### B. Steps

## 3. Right Tensioner

### A. Parts

| ID | Qty | Description |
|---|-----|---|
| PN013 | 1 | XY Tensioner, Tensioner Cap |
| PN014 | 1 | XY Tensioner, Guide Frame |
| PN508 | 3 | Screw, M3-0.5 x 40mm SHCS |
| PN532 | 2 | Screw, M5-0.8 x 12mm BHCS |
| PN534 | 3 | Screw, M5-0.8 x 25mm BHCS |
| PN577 | 4 | Washer, M5, Split Lock |

### B. Steps

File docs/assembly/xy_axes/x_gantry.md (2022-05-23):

---
title: X Gantry and Belts
summary: Instructions for the attaching the X Gantry and belts.
authors: Jon Harper
date: 2022-05-23
---

*This document is a placeholder until more content is generated.*

## 1. Gantry Carriage

### A. Parts

| ID | Qty | Description |
|---|-----|---|
| PN030 | 1 | X Gantry, Carriage Mount |
| PN031 | 1 | X Gantry, Top Mount |
| PN032 | 1 | X Gantry, Back Mount |
| PN033 | 1 | X Gantry, Front Mount |
| PN501 | 8 | Screw, M3-0.5 x 8mm SHCS |
| PN502 | 3 | Screw, M3-0.5 x 12mm SHCS |

### B. Steps

## 2. Belts

### A. Parts

| ID | Qty | Description |
|---|-----|---|
| PN612 | 2 | Belt, 2GT-2, 6mm, Fiberglass Core, 2m |

### B. Steps

## 3. Belt Clamps

### A. Parts

| ID | Qty | Description |
|---|-----|---|
| PN034 | 1 | X Gantry, L Belt Clamp |
| PN035 | 1 | X Gantry, R Belt Clamp |
| PN501 | 4 | Screw, M3-0.5 x 8mm SHCS |

### B. Steps

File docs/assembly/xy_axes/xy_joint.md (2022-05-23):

---
title: XY Joint
summary: Installation instructions for the XY joint.
authors: Jon Harper
date: 2022-05-22
---

*This document is a placeholder until more content is generated.*

## 1. Left Joint

### A. Parts

| ID | Qty | Description |
|---|-----|---|
| PN005 | 1 | XY Joint, L Top |
| PN006 | 1 | XY Joint, L Mid |
| PN007 | 1 | XY Joint, L Bottom |
| PN509 | 2 | Screw, M3-0.5 x 45mm SHCS |
| PN601 | 2 | Bearing, F695-2RS |
| PN610 | 1 | Idler Pulley, 2GT-2 20T, 5mm Bore |
| PN620 | 2 | Dowel Pin, 5mm OD, 25mm |

### B. Steps

## 2. Right Joint

### A. Parts

| ID | Qty | Description |
|---|-----|---|
| PN008 | 1 | XY Joint, R Top |
| PN009 | 1 | XY Joint, R Mid |
| PN010 | 1 | XY Joint, R Bottom |
| PN091 | 1 | Misc, Limit Switch Cap |
| PN093 | 1 | XY Motion, X Limit Switch Mount |
| PN501 | 1 | Screw, M3-0.5 x 8mm SHCS |
| PN503 | 1 | Screw, M3-0.5 x 16mm SHCS |
| PN504 | 1 | Screw, M3-0.5 x 20mm, SHCS |
| PN509 | 2 | Screw, M3-0.5 x 45mm SHCS |
| PN601 | 2 | Bearing, F695-2RS |
| PN610 | 1 | Idler Pulley, 2GT-2 20T, 5mm Bore |
| PN620 | 2 | Dowel Pin, 5mm OD, 25mm |
| PN910 | 1 | Limit Switch |

### B. Steps

## 3. Combine with Extrusion

### A. Parts

| ID | Qty | Description |
|---|-----|---|
| A5 | 1 | 2020 Extrusion, 440mm, Milled with Linear Rail |
| PN533 | 4 | Screw, M5-0.8 x 16mm BHCS |
| PN534 | 2 | Screw, M5-0.8 x 25mm BHCS |
| PN577 | 6 | Washer, M5, Split Lock |

### B. Steps

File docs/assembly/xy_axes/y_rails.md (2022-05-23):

---
title: Y Rail Alignment
summary: Instructions for attaching the X axis and aligning the Y rails.
authors: Jon Harper
date: 2022-05-22
---

*This document is a placeholder until more content is generated.*

## 1. Rail Stops

### A. Parts

| ID | Qty | Description |
|---|-----|---|
| PN099 | 2 | XY Motion, Y Axis Front Rail Guide  |
| PN532 | 2 | Screw, M5-0.8 x 12mm BHCS |
| PN577 | 2 | Washer, M5, Split Lock |

### B. Steps

## 2. Gantry Lock Bars

### A. Parts

| ID | Qty | Description |
|---|-----|---|
| PN094 | 2 | Misc, X Gantry Service Bar |
| PN532 | 4 | Screw, M5-0.8 x 12mm BHCS |
| PN574 | 4 | Tee Nut, 6mm Slot, M5, Drop In |

### B. Steps

## 3. X Axis Installation

### A. Parts

| ID | Qty | Description |
|---|-----|---|
| PN502 | 8 | Screw, M3-0.5 x 12mm SHCS |

### B. Steps

## 4. Rail Alignment

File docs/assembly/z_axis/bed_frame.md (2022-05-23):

---
title: Bed Frame Assembly
summary: Instructions on assembling the frame for the heated bed.
authors: Jon Harper
date: 2022-04-11
---

*This document is a placeholder until more content is generated.*

## Bed Frame Assembly

### A. Parts

### Parts

| ID | Qty | Description |
|---|-----|---|
| B1 | 1 | 2020 Extrusion, 220mm |
| B2 | 1 | 2020 Extrusion, 220mm |
| B3 | 1 | 2020 Extrusion, 350mm |
| B4 | 1 | 2020 Extrusion, 350mm |
| PN020 | 4 | Z Axis, Bed Corner Bracket |
| PN532 | 16  | Screw, M5-0.8 x 12mm BHCS |
| PN577 | 16  | Washer, M5, Split Lock |

### B. Steps

| Step | Example |
|---|---|
|

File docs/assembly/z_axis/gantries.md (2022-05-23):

---
title: Z Gantries
summary: Guide to installing the Z gantries and attaching the bed.
authors: Jon Harper
date: 2022-04-11
---

*This document is a placeholder until more content is generated.*

## 1. Attach the Gantry Carriages
### A. Parts

| ID | Qty | Description |
|---|-----|---|
| PN022 | 1 | Z Axis, R Gantry |
| PN021 | 1 | Z Axis, L Gantry |
| PN502 | 8 | Screw, M3-0.5 x 12mm SHCS |

### B. Steps

## 2. Prepare the Lead Screw Plates

### A. Parts

| ID | Qty | Description |
|---|-----|---|
| PN027 | 1 | Z Axis, L Lead Screw Plate |
| PN028 | 1 | Z Axis, R Lead Screw Plate |
| PN503 | 8 | Screw, M3-0.5 x 16mm SHCS |
| PN579 | 2 | Thumb Nut, M3 |
| PN505 | 2 | Screw, M3-0.5 x 25mm SHCS |
| PN643 | 2 | Lead Screw Nut, Tr8x4, Anti-Backlash |
<!--| PN570 | 8   | Hex Nut, M3                          |-->

### B. Steps

## 3. Attach the Bed

### A. Parts

| ID | Qty | Description |
|---|-----|---|
| PN501 | 4 | Screw, M3-0.5 x 8mm SHCS |
| PN532 | 12  | Screw, M5-0.8 x 12mm BHCS |
| PN577 | 12  | Washer, M5, Split Lock |

### B. Steps

## 4. Install Limit Switches

### A. Parts

| ID | Qty | Description |
|---|-----|---|
| PN025 | 1 | Z Motion, L Limit Switch Mount |
| PN026 | 1 | Z Motion, R Limit Switch Mount |
| PN091 | 2 | Misc, Limit Switch Cap |
| PN503 | 4 | Screw, M3-0.5 x 16mm SHCS |
| PN533 | 2 | Screw, M5-0.8 x 16mm BHCS |
| PN577 | 2 | Washer, M5, Split Lock |
| PN910 | 2 | Limit Switch |

### B. Steps

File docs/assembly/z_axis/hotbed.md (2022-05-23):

---
title: Heated Bed Installation
summary: Instructions on preparing and installing the heated bed.
authors: Jon Harper
date: 2022-05-23
---

*This document is a placeholder until more content is generated.*

## Prepare the Heated Bed

### A. Parts

| ID | Qty | Description |
|---|-----|---|
| PN550 | 4 | Screw, M4-0.7 x 35mm FHCS |
| PN571 | 4 | Hex Nut, M4 |
| PN812 | 1 | Heated Bed, 310x310mm |

### B. Steps

| Step | Example |
|---|---|

## Bed Leveling Plates

### A. Parts

| ID | Qty | Description |
|---|-----|---|
| PN029 | 1 | Z Axis, Bed Wire Support |
| PN530 | 6 | Screw, M5-0.8 x 8mm BHCS | <!-- TODO Add to BOM -->
<!--| PN532 | 8   | Screw, M5-0.8 x 12mm BHCS           |  TODO Remove from BOM -->
| PN532 | 2   | Screw, M5-0.8 x 12mm BHCS           |
| PN577 | 8   | Washer, M5, Split Lock              |
<!--| PN578 | 6   | Washer, M5 x 10mm                   |  TODO Remove from BOM -->
| PN813 | 4   | Idler Pulley Plate                  |

### B. Steps

| Step | Example |
|---|---|
| 

## Center Bed

### A. Parts

| ID | Qty | Description |
|---|-----|---|
| PN810 | 4 | Bed Spring |
| PN811 | 4 | Bed Leveling Nut |

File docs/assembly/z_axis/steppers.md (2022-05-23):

---
title: Stepper Installation
summary: Guide to installing Z steppers and lead screw guide.
authors: Jon Harper
date: 2022-04-11
---

*This document is a placeholder until more content is generated.*

## Steppers

### A. Parts

| ID | Qty | Description |
|---|-----|---|
| PN023 | 1 | Z Axis, L Stepper Mount |
| PN024 | 1 | Z Axis, R Stepper Mount |
| PN501 | 6 | Screw, M3-0.5 x 8mm SHCS |
| PN537 | 6 | Screw, M5-0.8 x 50mm BHCS |
| PN552 | 4\* | Screw, M4-0.7 x 16mm SHCS |
| PN577 | 6 | Washer, M5, Split Lock |
| PN581 | 2 | Coupler, 5mm to 8mm, Spider |
| PN901 | 2 | Stepper, NEMA 17, 39mm, 1.8 Degree, 1.5A |

\* Note: These screws are usually sold with the spider coupler and are also generally pre-installed.
### B. Steps

| Step | Example |
|---|---|
| "Fish" the six (6) pre-positioned M5 tee nuts under the Z extrusions to line up with the left stepper mount. | |
| Attach the stepper to the stepper mount with three (3) M3 x 8mm screws. The stepper wires or connector should be oriented towards the center of the printer. | |
| Arrange one of the two steppers under the left stepper mount. | |
| Prepare three (3) M5 x 50mm screws and lock washers. | |
| Position the stepper and mount under the pre-positioned tee nuts. | |
| Lightly thread each of the screws with lock washers into the tee nuts until all three are attached. | |
| Tighten the screws. | |
| Place the coupler on the installed stepper's drive shaft and tighten. | |
| Repeat the above steps for the right side. | |

## Alignment and Sealing Bearings

### A. Parts

| ID | Qty | Description |
|---|-----|---|
| PN095 | 2 | Bearing Alignment Slider, TPU |
| PN123 | 1 | L Z Slider Mount |
| PN124 | 1 | R Z Slider Mount |
| PN532 | 4 | Screw, M5-0.8 x 12mm BHCS |
| PN577 | 4 | Washer, M5, Split Lock |
| PN600 | 2 | Ball Bearing, F688ZZ |

### B. Steps

| Step | Example |
|---|---|
| Locate the two tee nuts that you will need to attach the left slider mount and pre-position them. | |
| Attach the left slider mount using two (2) M5 x 12mm screws and two lock washers. | |
| Insert an F588 bearing into an alignment slider and set it in the slider mount opening. | |
| Repeat for the rigth side. | |

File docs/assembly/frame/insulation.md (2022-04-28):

---
title: Prepare Insulation
summary: Pause to measure and install insulation.
authors: Jon Harper
date: 2022-04-07
---

*This document is actively being refined and edited for mistaeks.*

!!! note
    In this section we will be cutting polyisocyanurate foam (PIR foam, often called "polyiso"). Several tips:

    - PIR foam tears easily, so use a blade with a straight edge.
    - Additionally, the aluminum radiant barrier on one side is very thin and tears easily. You will need a sharp blade to get a clean cut.
    - When in doubt, cut wide and pare down to fit in place later.
    
!!! caution
    - Do not try to make a crease on side and cut the other: the crease that appears on the uncut part of the foam will not align with the precut area. Instead cut halfway, then cut a second or third time more deeply over the first until breaking through.
    - Use a piece of cardboard underneath the foam to avoid cutting anything important underneath the foam and/or damaging your blade.

## A. Materials

| Parts | Description |
|---|---|
| MN003 | VHB Tape, Double-Sided, 1" Width |
| MN100 | Polyisocyanurate Foam, 1/2", 4'x8' sheet |

## B. General Procedure

All of the insulation pieces follow the same general procedure of laying out the frame, marking, and cutting. To illustrate:

| Step | Example |
|---|---|
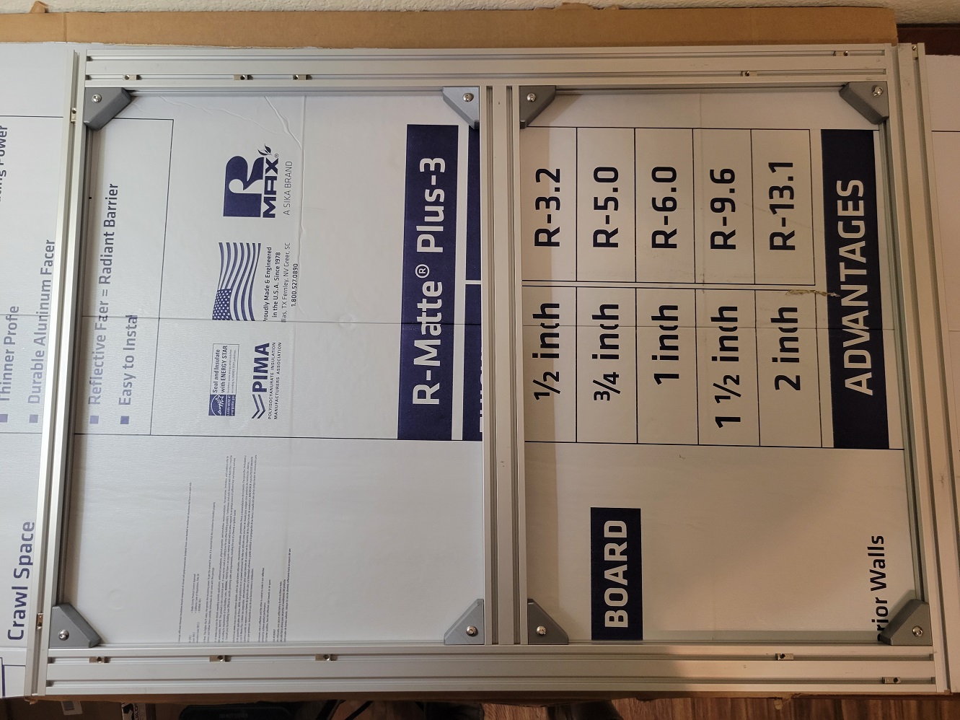
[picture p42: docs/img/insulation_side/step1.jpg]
lay out the insulation
| Lay out |  |
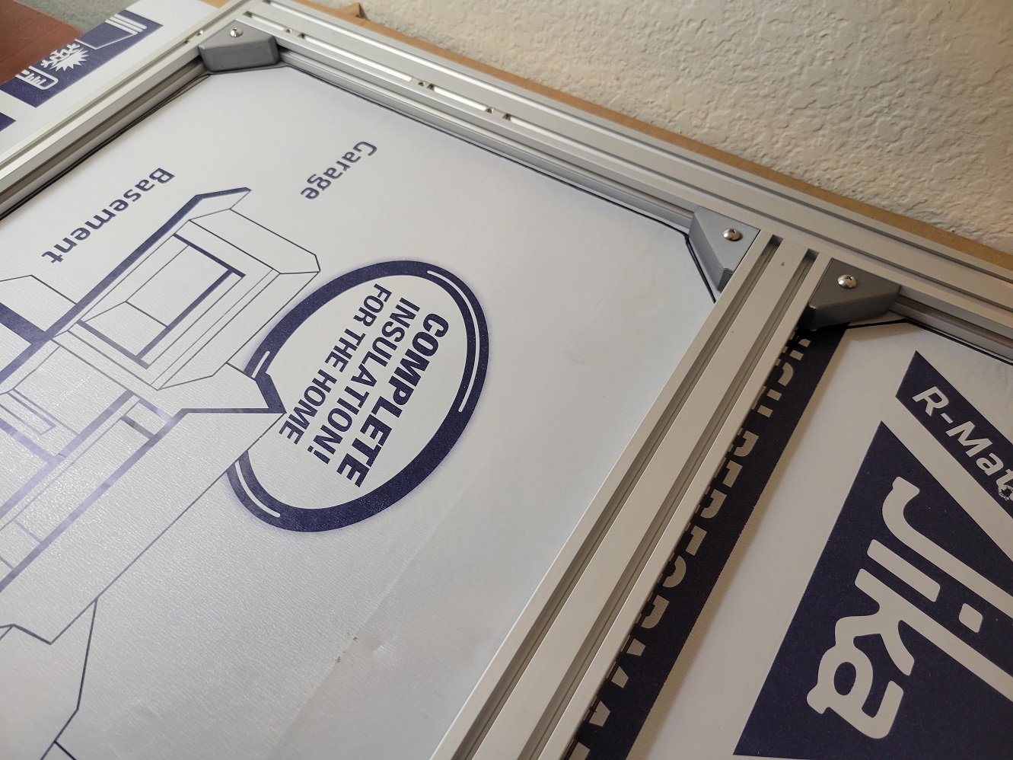
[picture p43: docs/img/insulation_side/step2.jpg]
lay out the insulation
| Mark at least twice around |  |
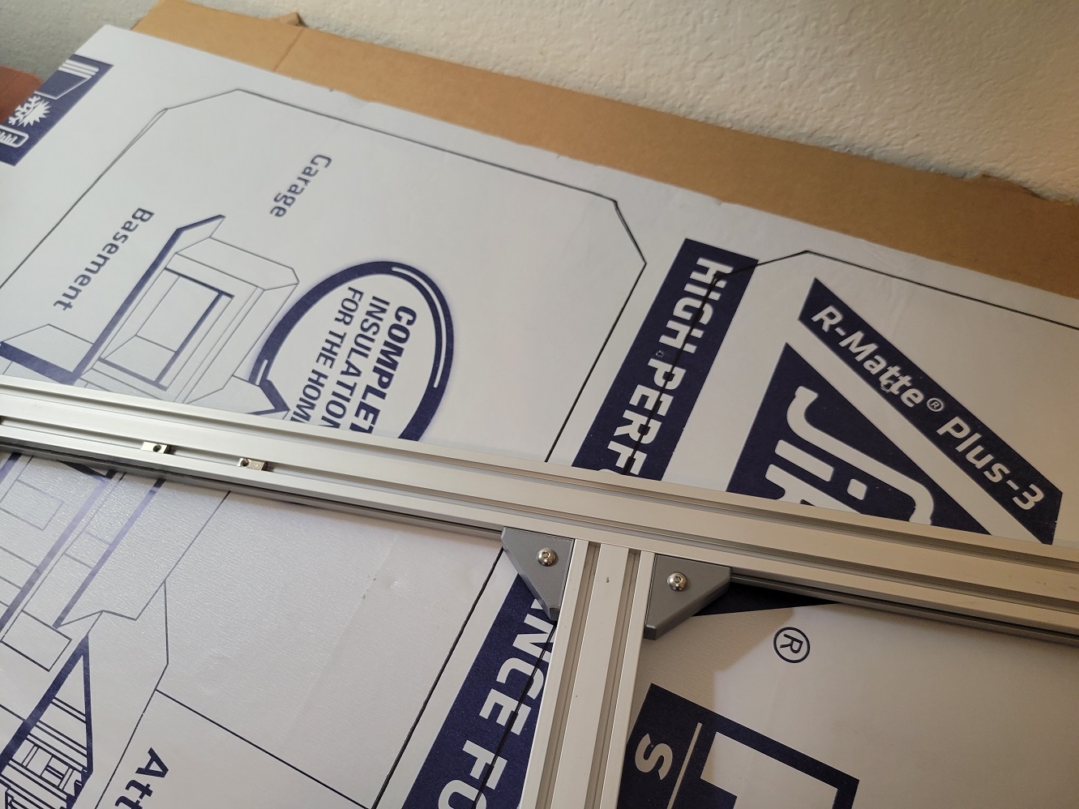
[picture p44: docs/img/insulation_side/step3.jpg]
lay out the insulation
| Remove the frame and cut carefully. |  |

## C. Mark Side Panels

1. Turn the frame on its side.
2. Lay a ~2'/600 wide strip of PIR foam across the side panel
3. Put something slightly heavy on top to keep it pressed down.
4. Draw an outline of the inside of the frame on the insulation. Do this for both halves.
5. Repeat the outline several times to ensure it covers at much area as possible.
6. Set aside on a flat surface and carefully cut the insulation.

## D. Mark Rear Panel

1. Leave the frame on its side.
2. Cut a strip slightly wider than 2'/600mm of PIR foam.
3. Use something heavy to press it firmly against the back of the frame (or push against a wall).
4. Mark an outline of the inside of the frame on the insulation, repeating twice.
5. Set aside on a flat surface and carefully cut the insulation.

## E. Mark Top Panel

1. Cut a 2'/600mm wide strip of PIR foam insulation.
2. Press firmly against the top of the frame.
3. Mark an outline of the frame and brackets, repeating twice.
4. Set aside on a flat surface and carefully cut the insulation.

## F. Floor Cover Insulation

1. Mark two (2) 40mm x 300mm strips of insulation.
2. Mark two (2) 40mm x 140mm strips of insulation.
3. Cut each strip individually.
5. Place a piece of VHB tape on each the 140mm strips.
6. Place a piece of VHB tape on both ends of each of the 300mm strips.
7. Attach to the underside of the floor cover.

## G. Floor Hatch Insulation

## TODO

Link guides on cutting insulation

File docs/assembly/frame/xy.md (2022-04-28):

---
title: XY Framing
summary: Instructions on assembling the XY framing.
authors: Jon Harper
date: 2022-04-15
---

*This document is actively being refined and edited for mistaeks.*

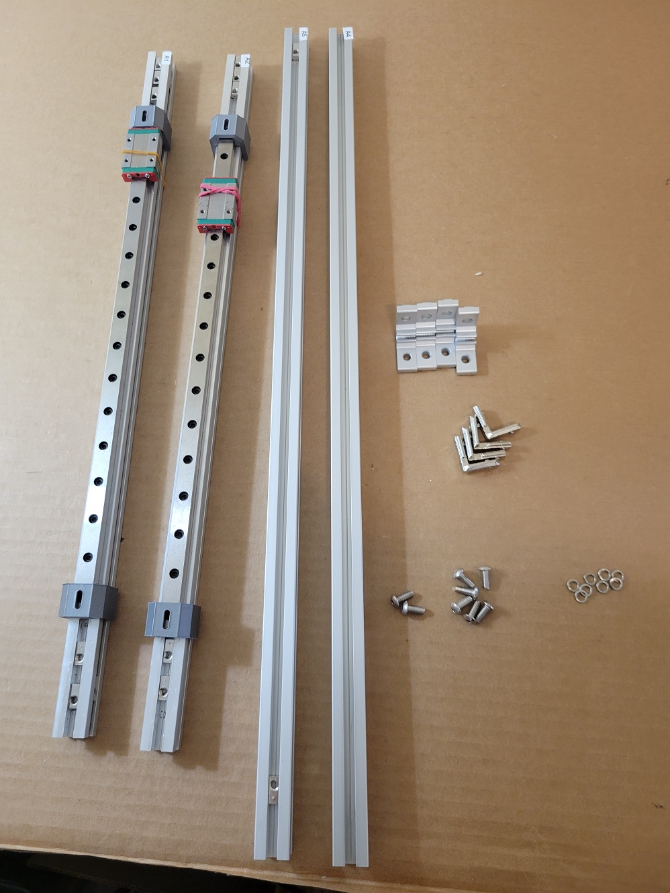
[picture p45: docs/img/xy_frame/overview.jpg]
overview of parts


## 1. Assemble XY Frame

### A. Parts

| ID | Qty | Description | Notes |
|---|-----|---|---|
| A1 | 1 | 2020 Extrusion, 440mm, Milled | |
| A2 | 1 | 2020 Extrusion, 440mm, Milled | |
| A4 | 1 | 2020 Extrusion, 620mm | |
| A5 | 1 | 2020 Extrusion, 620mm | |
| PN502 | 8 | Screw, M3-0.5 x 12mm SHCS | |
| PN556 | 8 | Set Screw, M4-0.7 x 4mm | Usually comes installed in PN701 |
| PN577 | 8 | Washer, M5, Split Lock | |
| PN700 | 4 | Corner Bracket, Tapped | |
| PN701 | 4 | Corner Bracket, Inside Hidden | |

### B. Install Hidden Corner Brackets

| Step | Example |
|---|---|
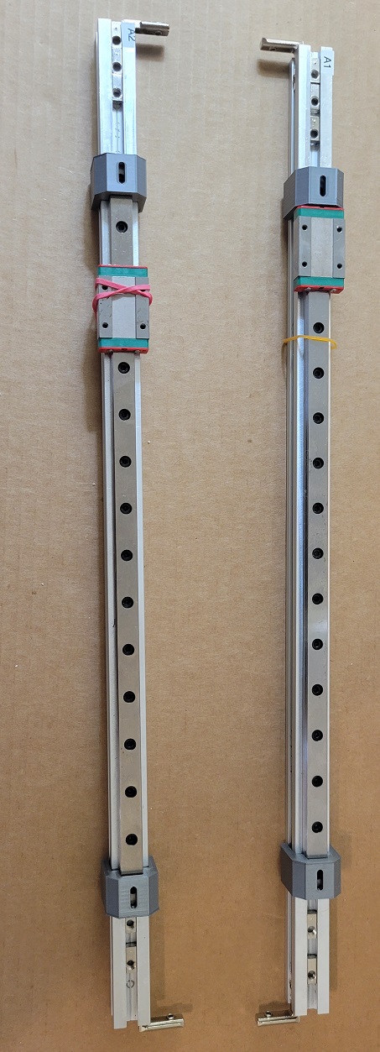
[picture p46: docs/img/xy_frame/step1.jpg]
step 1
| Install brackets as pictured. Note the orientation of the frame guides. |  |
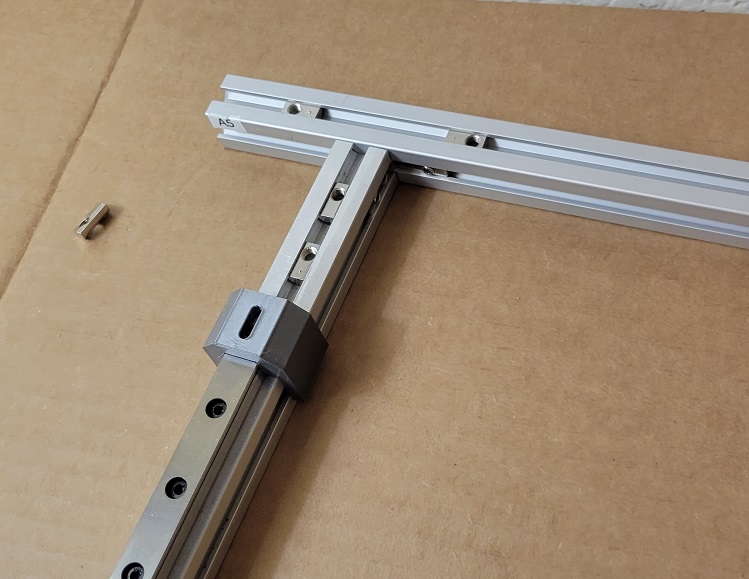
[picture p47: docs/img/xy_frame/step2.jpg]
step 2
| Slide A1 into A4 and A5 from the left. You will need to remove one tee nut each on A4 and A5. |  |
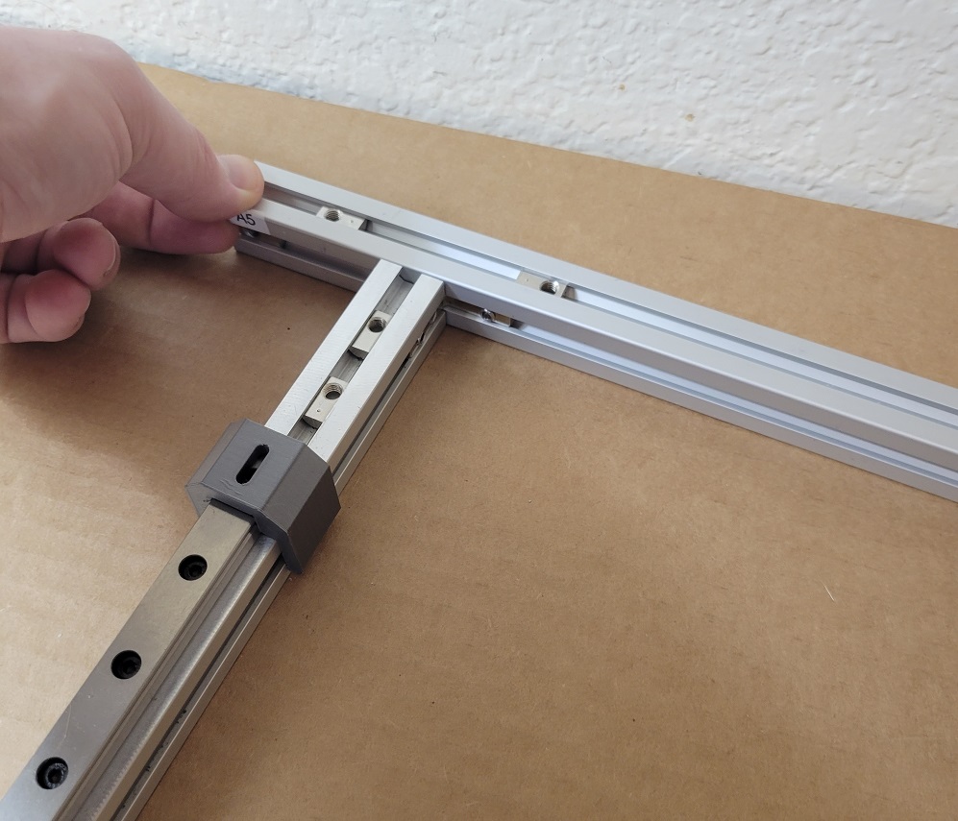
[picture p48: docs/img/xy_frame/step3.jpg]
step 3
| Reinsert the tee nuts! |  |
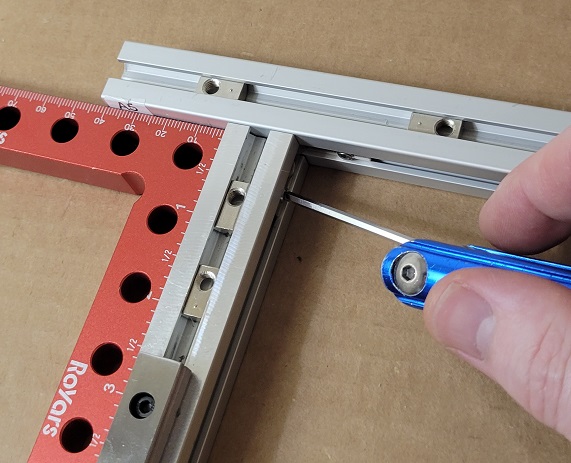
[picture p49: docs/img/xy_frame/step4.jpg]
step 4
| Square and tighten. |  |

### C. Install Tapped Corner Brackets

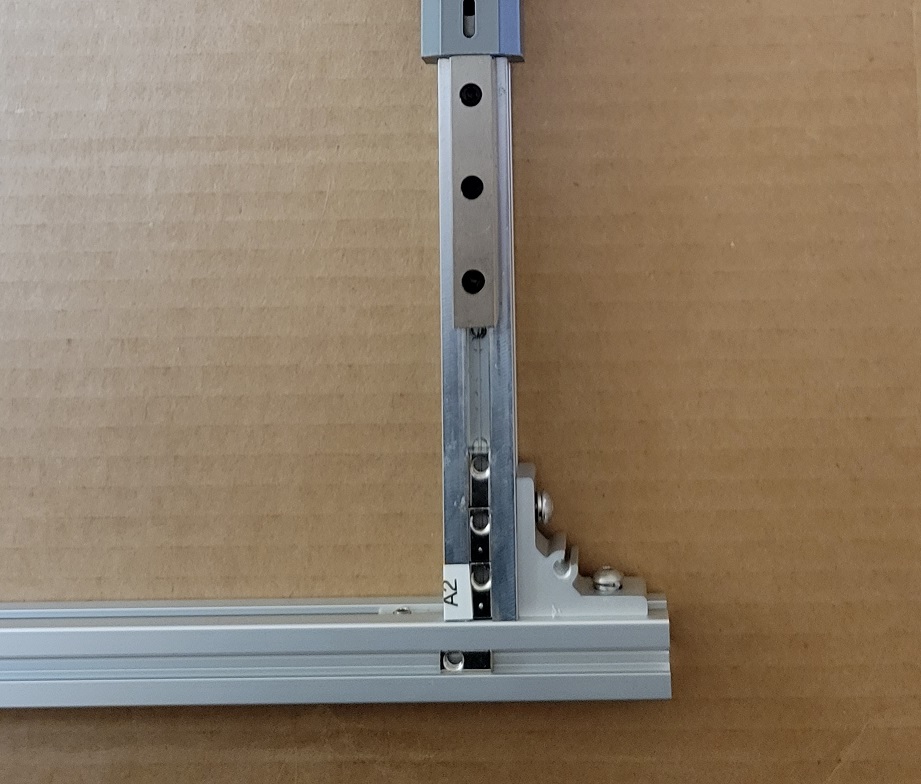
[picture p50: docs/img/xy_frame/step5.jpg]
installed brackets


Each inside hidden bracket has a matching tapped corner bracket on the other side of the extrusion. Follow the usual procedure for attaching and squaring a corner bracket for all four.

## 2. Prepare Brackets

### Parts

| ID | Qty | Description |
|---|-----|---|
| PN502 | 10  | Screw, M3-0.5 x 12mm SHCS |
| PN577 | 10  | Washer, M5, Split Lock |
| PN700 | 10  | Corner Bracket, Tapped |

### A. Attach Brackets to XY Frame

### B. Attach Brackets to Z Extrusions

### C. Attach Brackets to Sides

## 3. Square and Tighten

### Parts

| ID | Qty | Description |
|---|-----|---|
| PN502 | 10  | Screw, M3-0.5 x 12mm SHCS |
| PN577 | 10  | Washer, M5, Split Lock |

### A. Set XY Frame in Place

### B. Square and Measure

### C. Tighten

## 4. Add Bracket Covers

### Parts

| ID | Qty | Description |
|---|-----|---|
| PN090 | 14  | Corner Bracket Cover |
| PN530 | 14  | Screw, M5-0.8 x 8mm BHCS |

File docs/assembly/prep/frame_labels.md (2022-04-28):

---
title: Frame Labels
summary: Instructions on identifying frame components.
authors: Jon Harper
date: 2022-04-07
---

We've mentioned that each part of the frame has a unique ID to help identification and positioning. Let's label those now.

For your convenience, you can click any image to enlarge or use the [PDF version of this page](../../pdf/frame_labels.pdf).

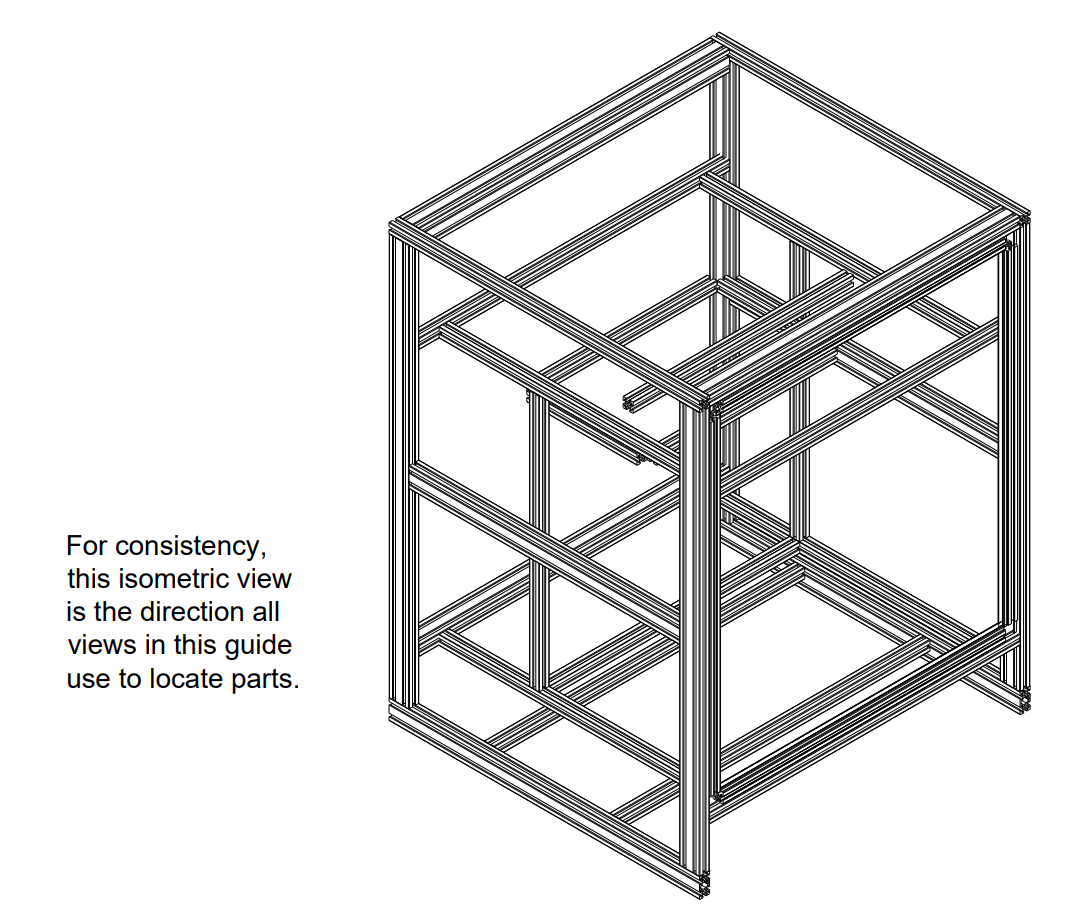
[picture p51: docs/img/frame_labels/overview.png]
Overview


!!! note "Musical Interlude"
    We're listening to The Heavy right now. Just sayin'.

## Instructions

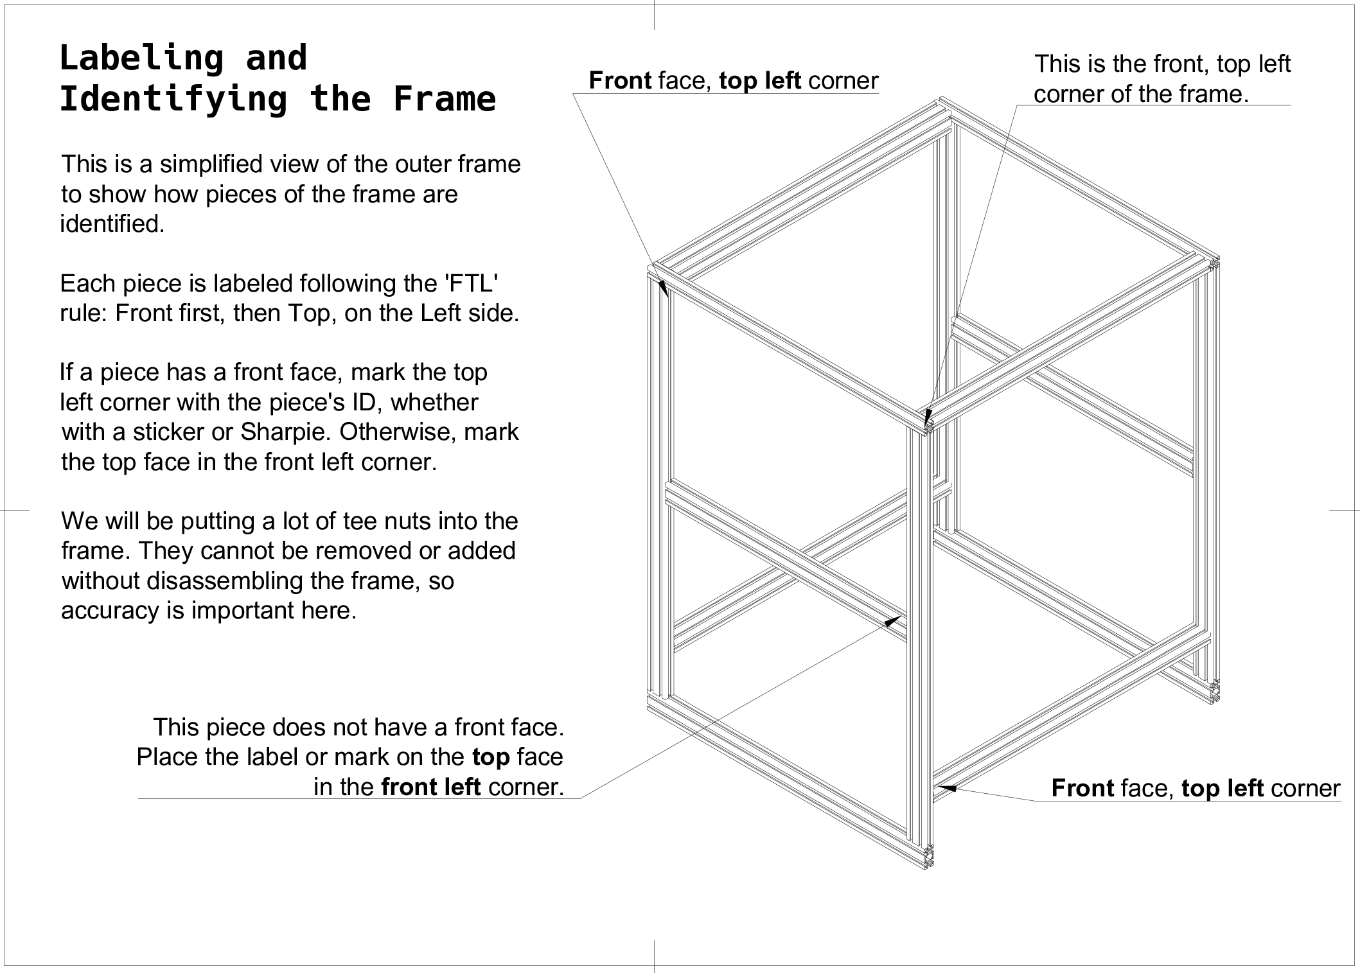
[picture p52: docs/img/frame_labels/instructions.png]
Labeling Instructions


## Frame Sections

### A. XY Axes

| ID | Part Number | Description |
|----|---|---|
| A1 | PN726 | 2020 Extrusion, 540mm, Milled |
| A2 | PN726 | 2020 Extrusion, 540mm, Milled |
| A3 | PN725 | 2020 Extrusion, 440mm, Milled |
| A4 | PN727 | 2020 Extrusion, 620mm |
| A5 | PN727 | 2020 Extrusion, 620mm |

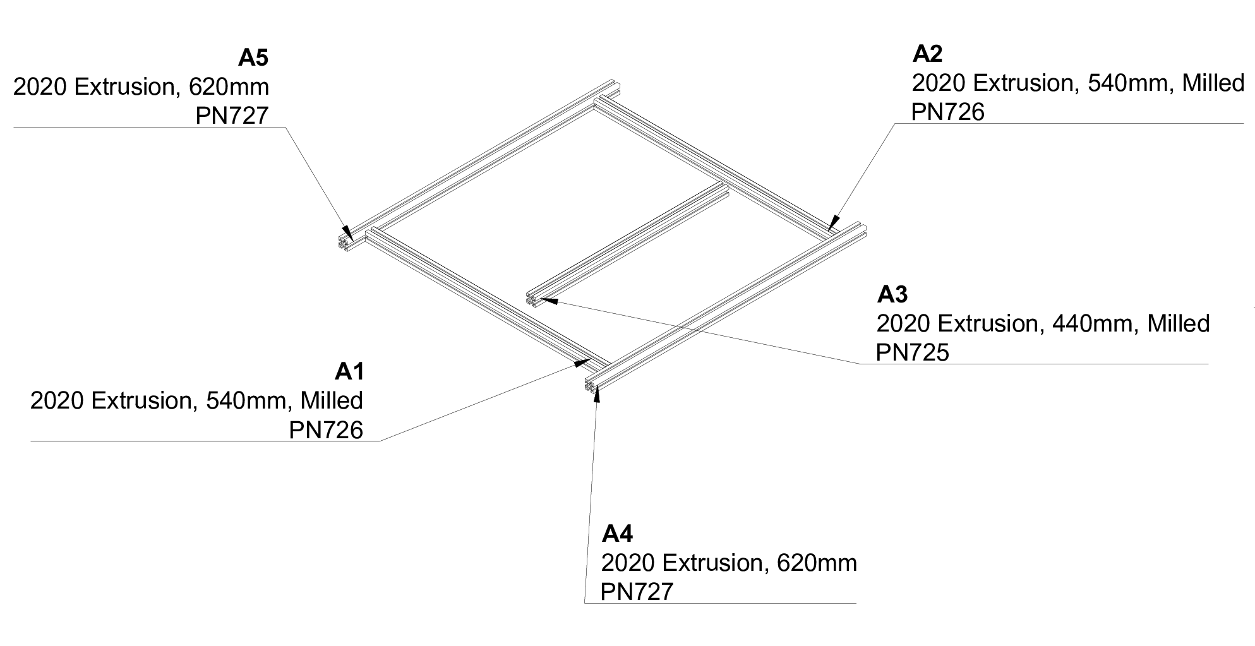
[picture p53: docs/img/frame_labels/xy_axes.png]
XY Axes Callouts


### B. Bed Frame

| ID | Part Number | Description |
|----|---|---|
| B1 | PN732 | 2020 Extrusion, 220mm |
| B2 | PN732 | 2020 Extrusion, 220mm |
| B3 | PN733 | 2020 Extrusion, 350mm |
| B4 | PN733 | 2020 Extrusion, 350mm |

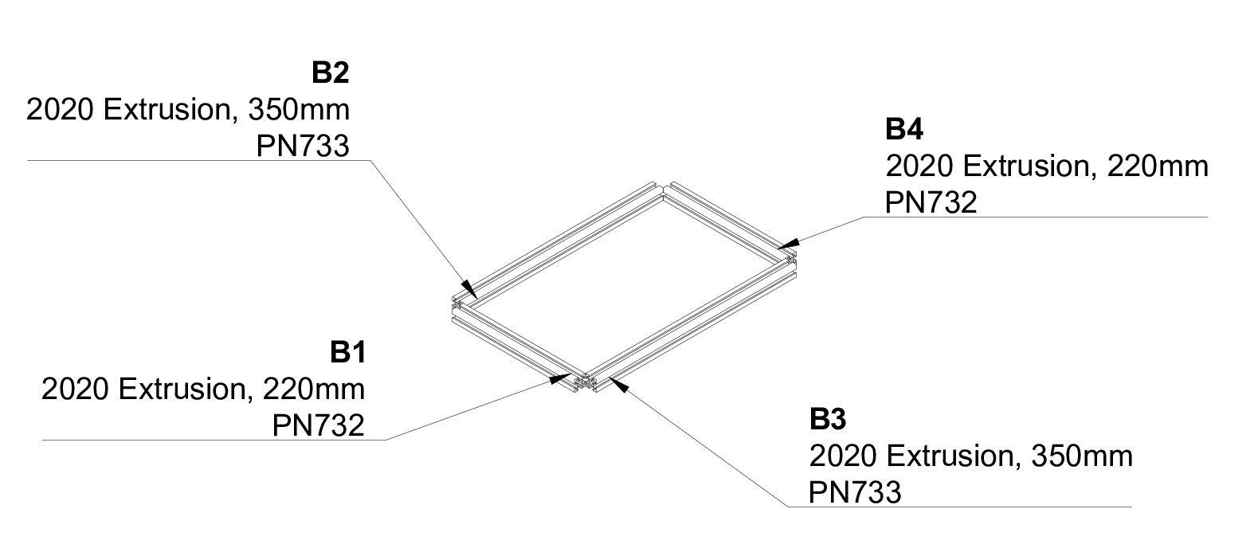
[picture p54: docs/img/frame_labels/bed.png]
Bed Frame Callouts


### C. Crossbars

| ID | Part Number | Description |
|----|---|---|
| C1 | PN750 | 404020 Extrusion, 620mm |
| C2 | PN750 | 404020 Extrusion, 620mm |
| C3 | PN741 | 2040 Extrusion, 620mm |
| C4 | PN741 | 2040 Extrusion, 620mm |

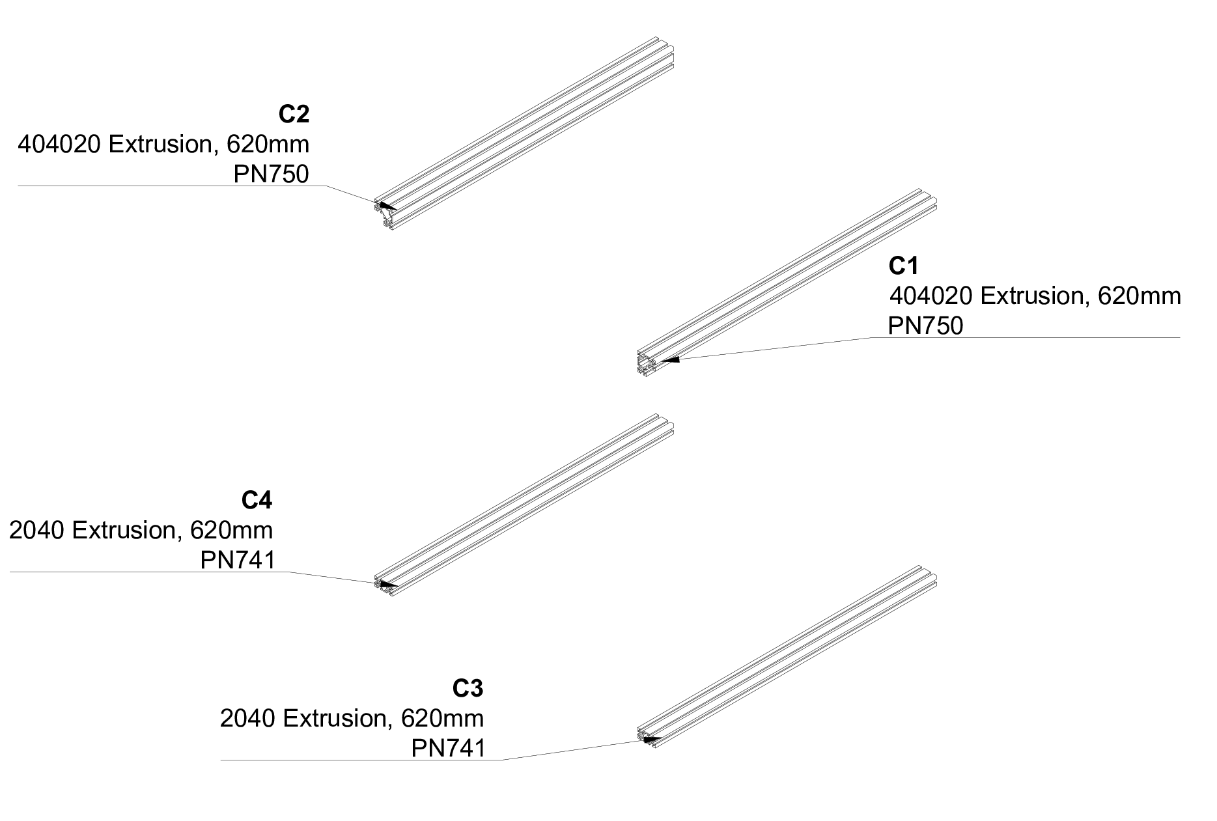
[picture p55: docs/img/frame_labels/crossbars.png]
Crossbar Callouts


### D. Door

| ID | Part Number | Description |
|----|---|---|
| D1 | PN751 | 2020 Door Extrusion, 564mm |
| D2 | PN751 | 2020 Door Extrusion, 564mm |
| D3 | PN752 | 2020 Door Extrusion, 646mm |
| D4 | PN752 | 2020 Door Extrusion, 646mm |

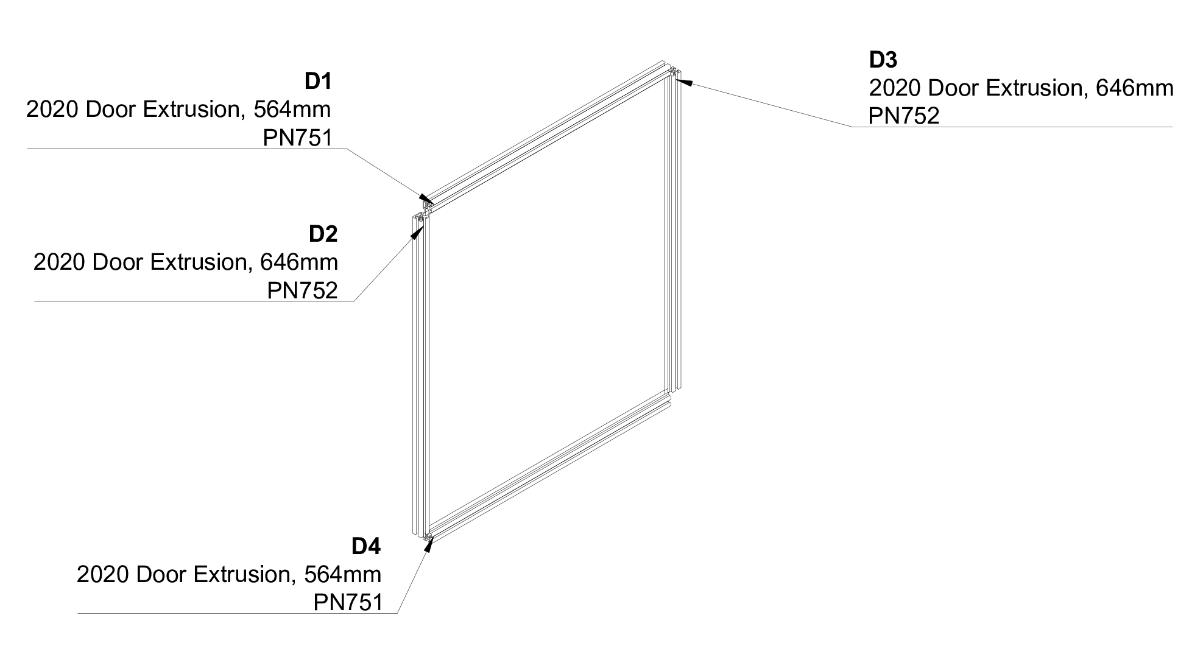
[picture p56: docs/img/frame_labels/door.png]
Door Callouts


### E. Electronics Mounting Bars

| ID | Part Number | Description |
|----|---|---|
| E1 | PN727 | 2020 Extrusion, 620mm |
| E2 | PN727 | 2020 Extrusion, 620mm |

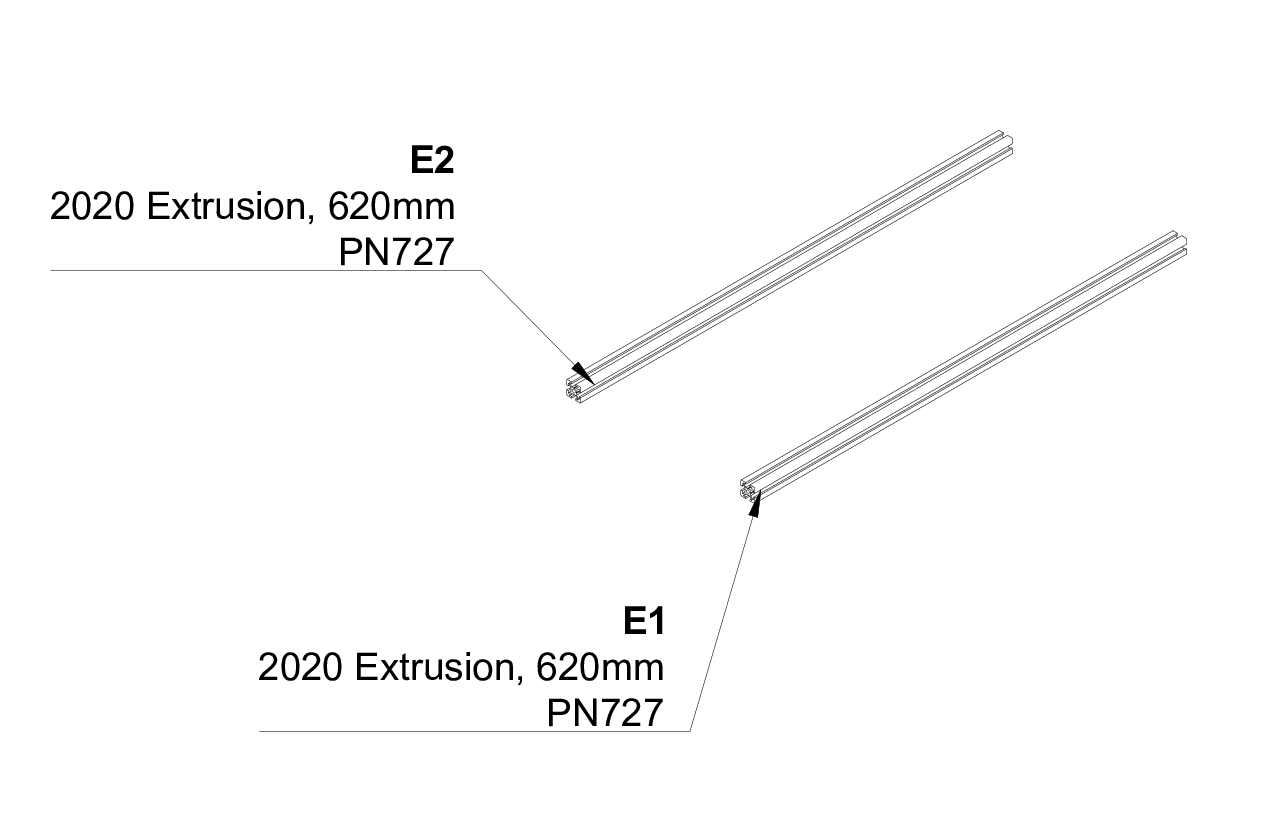
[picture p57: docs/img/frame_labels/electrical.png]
Electrical Callouts


### F. Left Side

| ID | Part Number | Description |
|----|---|---|
| L1 | PN727 | 2040 Extrusion, 620mm |
| L2 | PN741 | 2040 Extrusion, 620mm |
| L3 | PN740 | 2040 Extrusion, 800mm |
| L4 | PN740 | 2040 Extrusion, 800mm |
| L5 | PN742 | 2040 Extrusion, 540mm |

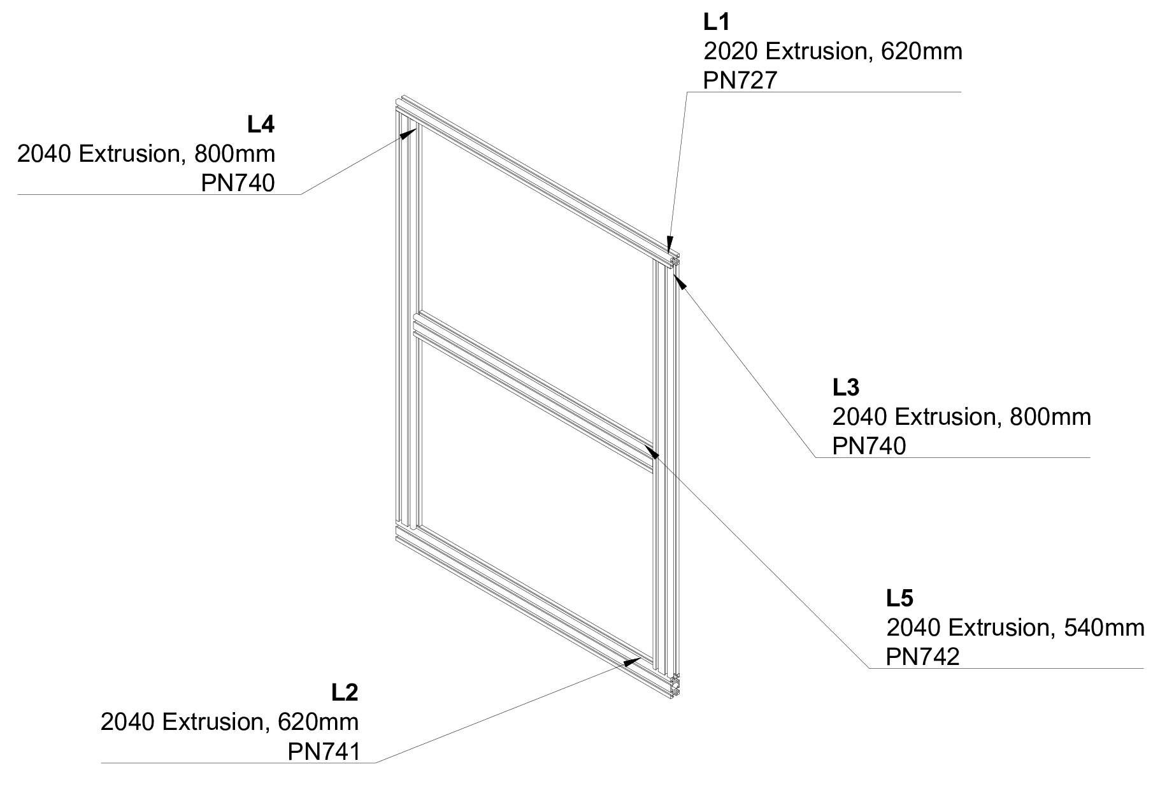
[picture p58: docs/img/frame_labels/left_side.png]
Left Side Callouts


### G. Right Side

| ID | Part Number | Description |
|----|---|---|
| R1 | PN727 | 2040 Extrusion, 620mm |
| R2 | PN741 | 2040 Extrusion, 620mm |
| R3 | PN740 | 2040 Extrusion, 800mm |
| R4 | PN740 | 2040 Extrusion, 800mm |
| R5 | PN742 | 2040 Extrusion, 540mm |

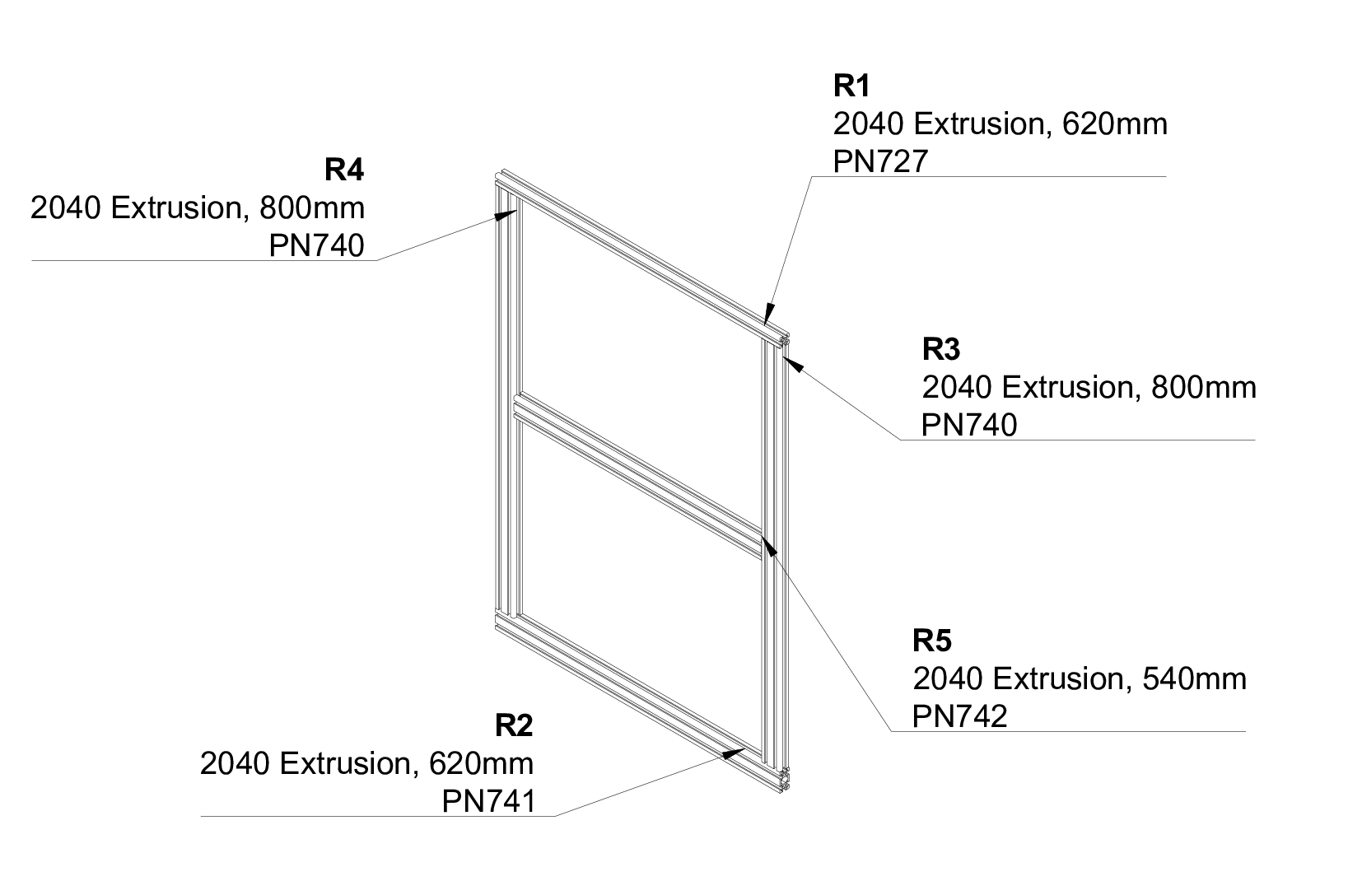
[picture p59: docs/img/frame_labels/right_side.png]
Right Side Callouts


### H. Z Axis

| ID | Part Number | Description |
|----|---|---|
| Z1 | PN729 | 2020 Extrusion, 510mm |
| Z2 | PN729 | 2020 Extrusion, 510mm |
| Z3 | PN730 | 2020 Extrusion, 540mm |
| Z4 | PN730 | 2020 Extrusion, 540mm |
| Z5 | PN728 | 2020 Extrusion, 500mm |

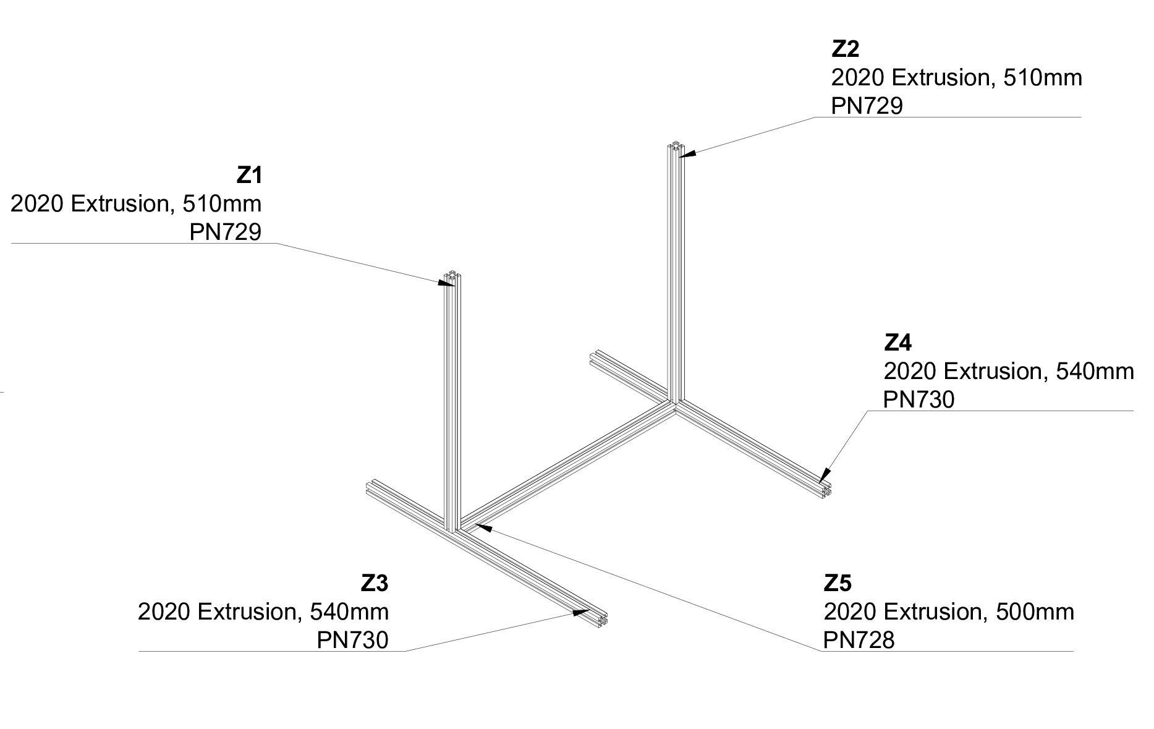
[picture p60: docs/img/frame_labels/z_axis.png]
Z Axis Callouts


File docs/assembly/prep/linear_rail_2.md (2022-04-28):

---
title: Z Axis Linear Rail Alignment
summary: Instructions on initial installation of the linear rails.
authors: Jon Harper
date: 2022-04-07
---

*This document is actively being refined and edited for mistaeks.*

At this point, all of our linear rails should be attached to an extrusion. The Z rails are aligned along the Z1 and Z2 extrusions with a bracket at the bottom. We need that bracket positioned when we assemble the frame, so we'll go ahead and lock down the rail, too.

## Parts

| ID | Qty | Description |
|---|----:|---|
| Z1 | 1 | PN729 with Linear Rail |
| Z2 | 1 | PN729 with Linear Rail |
| PN019 | 2 | Lower Rail Bracket |
| PN532 | 2 | Screw, M5-0.8 x 12mm BHCS |
| PN577 | 2 | Washer, M5, Split Lock |

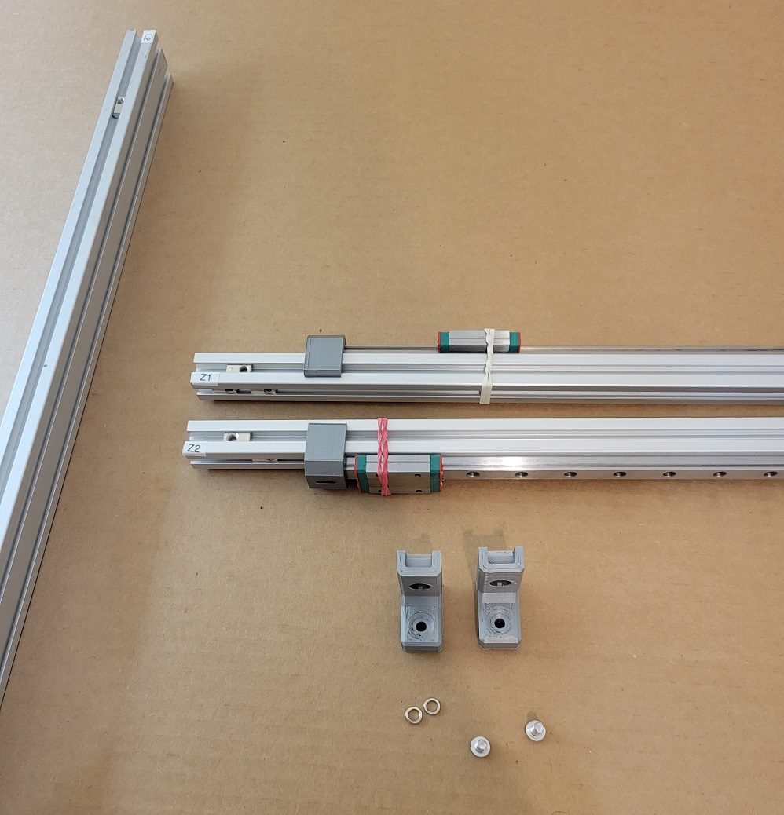
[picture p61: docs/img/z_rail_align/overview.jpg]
parts


## Assembly
### A. Place Bracket

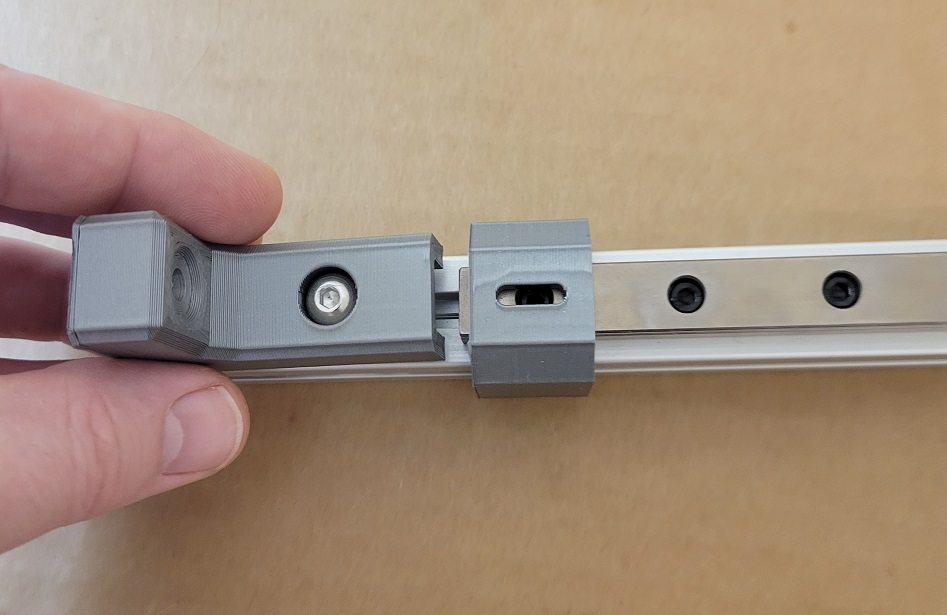
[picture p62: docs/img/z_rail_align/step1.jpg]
place the bracket


1. Insert a lock washer and screw into one of the brackets.
2. Set the bracket assembly on the *lower* end of the extrusion (following the FTL labeling rule)
3. Line the base of the bracket up roughly with the edge of the extrusion
4. Lightly secure the screw

### B. Align

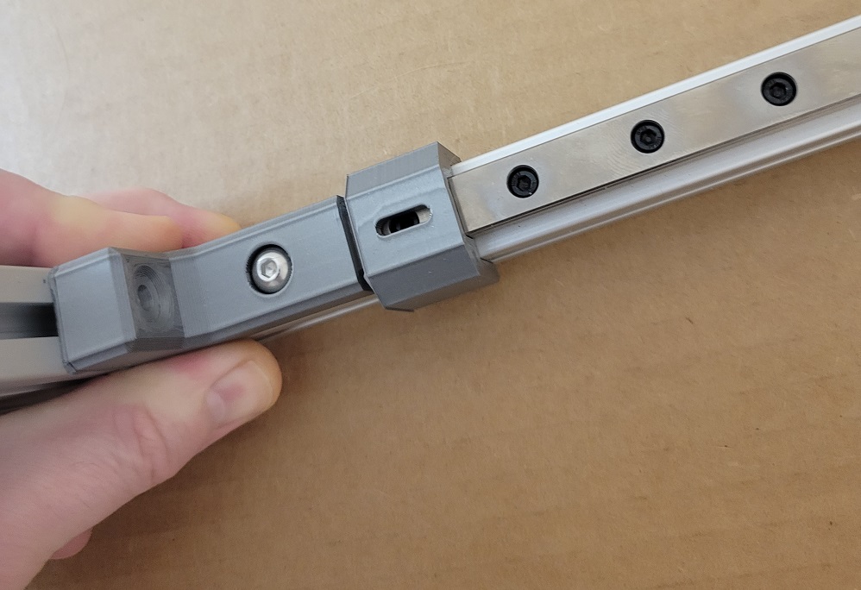
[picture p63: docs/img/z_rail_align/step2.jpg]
aligning with a 2040 extrusion


1. Place a square or another piece of extrusion at the bottom of the bracket.
2. Firmly press on the assembly to ensure alignment.
3. Tighten the bracket in place.

### C. Position Linear Rail

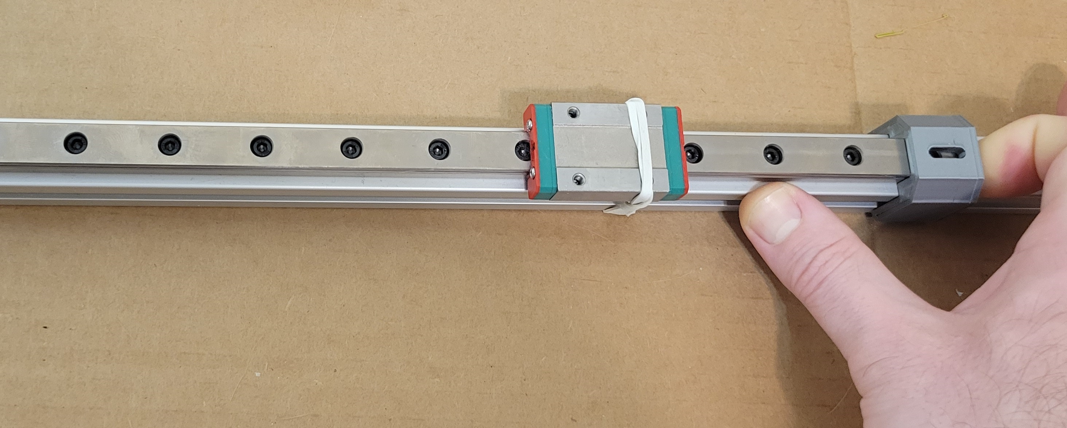
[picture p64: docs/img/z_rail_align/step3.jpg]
pushing the rail in place


1. Push the linear rail into the new bracket.
2. The bracket is a fairly tight fit; you may have to work it into place.

### D. Tighten the Rail

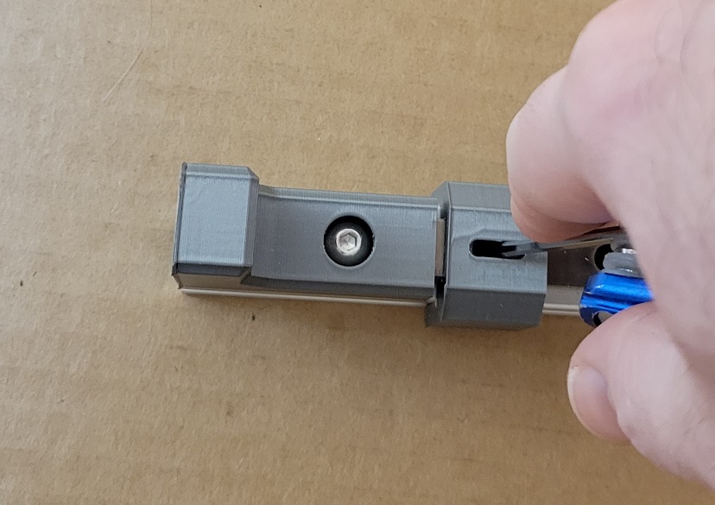
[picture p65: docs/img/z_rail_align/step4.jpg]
locking the rail in place


1. Check that both of the alignment brackets are flat to the rail with a good grip to center the rail.
2. Tighten the first and last screws on the extrusion, using the alignment bracket peephole if needed (see image).

### E. Repeat with Z2

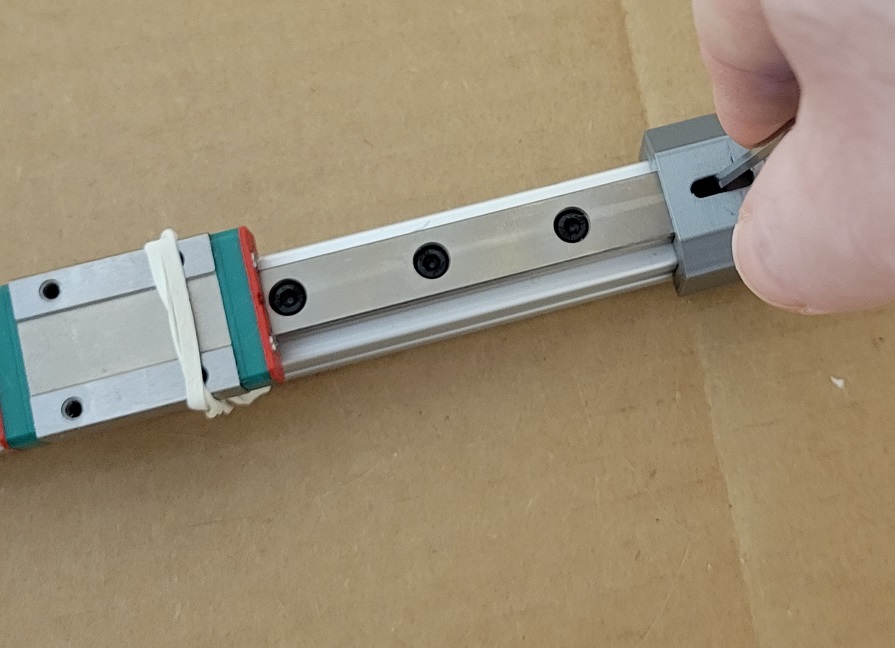
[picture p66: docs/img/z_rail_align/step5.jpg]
random picture


Lastly, repeat the process for the Z2 rail and extrusion.

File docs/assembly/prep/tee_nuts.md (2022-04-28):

---
title: Roll-In Tee Nut Installation
summary: Instructions on initial installation of the linear rails.
authors: Jon Harper
date: 2022-04-07
---

!!! note "Musical Suggestion"
    May we suggest [The Alan Parsons Project](https://youtube.com/playlist?list=OLAK5uy_lNCAUSEhegqjQAMMocw1QFu9G-bE4zeTM)?

There are a lot of tee nuts. Thankfully, this goes quickly with the extrusions labeled. The list below is fairly straightforward: the ID of the extrusion, the number of tee nuts needed, and a picture of roughly where each te`e nut goes. Click or tap the image to zoom in.
    
!!! attention
    - The tee nuts only need to be in the right channel and roughly in the right place. We will position them more precisely later.
    - Orientation only matters when a tee nut is near the edge of an extrusion. When a tee nut is very near the edge, put the roller bearing end in first. See [A3](../../img/tee_nuts/A3.jpg) for an example. Note that the hole is closer to the outer edge.

## Part List

Rather than a table, we'll use a short list:

- Every extrusion
- 275x PN575, Tee Nut, 6mm Slot, M5, Roll In (all of them)

## 1. XY Axis

| Extrusion | PN575 | Image |
|---|---|---|
| A1 | 11 | Extrusion A1 |
| A2 | 11 | Extrusion A2 |
| A3 | 6  | Extrusion A3 |
| A4 | 6  | Extrusion A4 |
| A5 | 11 | Extrusion A5 |

## 2. Bed

| Extrusion | PN575 | Image |
|---|---|---|
| B1 | 10 | Extrusion B1 |
| B2 | 10 | Extrusion B2 |
| B3 | 8  | Extrusion B3 |
| B4 | 8  | Extrusion B4 |

## 3. Frame Crossbars

| Extrusion | PN575 | Image |
|---|---|---|
| C1 | 6  | Extrusion C1 |
| C2 | 9  | Extrusion C2 |
| C3 | 14 | Extrusion C3 |
| C4 | 14 | Extrusion C4 |

## 4. Door

There's only one slot to insert tee nuts on these extrusions, so they're all in one image.

| Extrusion | PN575 | Image |
|---|---|---|
| D1, D2, D3, D4 | 2, 4, 2, 2 | Extrusion D1 |

## 5. Electrical Mounting Bars

| Extrusion | PN575 | Image |
|---|---|---|
| E1 | 4 | Extrusion E1 |
| E2 | 4 | Extrusion E2 |

## 6. Left External Frame

| Extrusion | PN575 | Image |
|---|---|---|
| L1 | 6  | Extrusion L1 |
| L2 | 8  | Extrusion L2 |
| L3 | 14 | Extrusion L3 |
| L4 | 11 | Extrusion L4 |
| L5 | 4  | Extrusion L5 |

## 7. Right External Frame

| Extrusion | PN575 | Image |
|---|---|---|
| R1 | 6  | Extrusion R1 |
| R2 | 8  | Extrusion R2 |
| R3 | 11 | Extrusion R3 |
| R4 | 11 | Extrusion R4 |
| R5 | 4  | Extrusion R5 |

## 8. Z Axis

!!! note
    Z1 and Z2 have a bracket already installed in the photo. For now, just install a tee nut there.

| Extrusion | PN575 | Image |
|---|---|---|
| Z1 | 7  | Extrusion Z1 |
| Z2 | 5  | Extrusion Z2 |
| Z3 | 15 | Extrusion Z3 |
| Z4 | 14 | Extrusion Z4 |
| Z4 | 10 | Extrusion Z5 |

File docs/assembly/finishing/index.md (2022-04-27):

---
title: Last Steps
summary: Finals steps to complete assembly
authors: Jon Harper
date: 2022-04-11
---

*This document is a placeholder until more content is generated.*

- Door
- Panels

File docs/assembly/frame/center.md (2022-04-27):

---
title: Joining the Halves
summary: How to assemble the two halves of the frame with center crosspieces.
authors: Jon Harper
date: 2022-04-13
---

*This document is actively being refined and edited for mistaeks.*

## 1. Left Side

We will start attaching crossbars to the left side first.

### Parts

| ID | Qty | Description |
|---|-----|---|
| C1 | 1 | 404020 Extrusion, 620mm |
| C2 | 1 | 404020 Extrusion, 620mm |
| C3 | 1 | 2040 Extrusion, 620mm |
| C4 | 1 | 2040 Extrusion, 620mm |
| PN532 | 8 | Screw, M5-0.8 x 12mm BHCS |
| PN533 | 4 | Screw, M5-0.8 x 16mm BHCS |
| PN577 | 12  | Washer, M5, Split Lock |
| PN700 | 4 | Corner Bracket, Tapped |
| PN702 | 2 | Corner Bracket, Super Thick, Tapped |

### A. Build the Base

Lay the left side of the frame flat.

### B. Top Crossbars

1. Start with C1 and attach it to the left side with two corner brackets.
2. Square and tighten.
3. Repeat with C2.

### C. Bottom Crossbars

1. Using calipers, a tape measure, or some other measuring device, attach a super thick bracket to C3 so that the top of the bracket is 120mm from the bottom of the L3 extrusion.
2. Attach C3 to L3 and square.
3. Repeat 1 and 2 with L4 and C4.

## 2. Adding in the Right Side

### Parts

| ID | Qty | Description |
|---|-----|---|
| PN532 | 8 | Screw, M5-0.8 x 12mm BHCS |
| PN533 | 4 | Screw, M5-0.8 x 16mm BHCS |
| PN577 | 12  | Washer, M5, Split Lock |
| PN700 | 4 | Corner Bracket, Tapped |
| PN702 | 2 | Corner Bracket, Super Thick, Tapped |

### A. Position the Right Side

Place the right side over the assembled left and center frame.

### B. Top Crossbars

1. Attach C1 to the right side with two corner brackets.
2. Square and tighten.
3. Repeat with C2.

### C. Bottom Crossbars

1. As above, attach a super thick bracket to C3 so that the top of the bracket is 120mm from the bottom of the R3 extrusion.
2. Square and tighten.
3. Repeat 1 and 2 with R4 and C4.

## 3. Bracket Covers

The eight brackets attaching C1 and C2 to the sides will need covers. As usual, the screws need to face inwards.

### Parts

| ID | Qty | Description |
|---|-----|---|
| PN090 | 8 | Corner Bracket Cover |
| PN530 | 8 | Screw, M5-0.8 x 8mm BHCS |

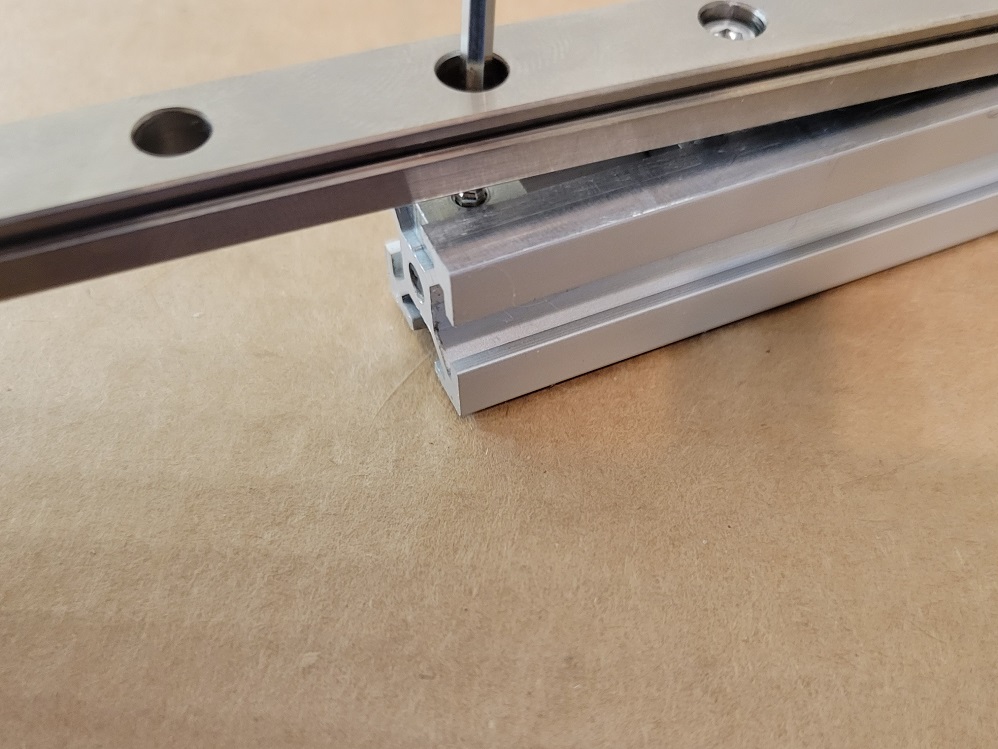
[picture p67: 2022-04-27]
docs/img/rail_install/oops2.jpg

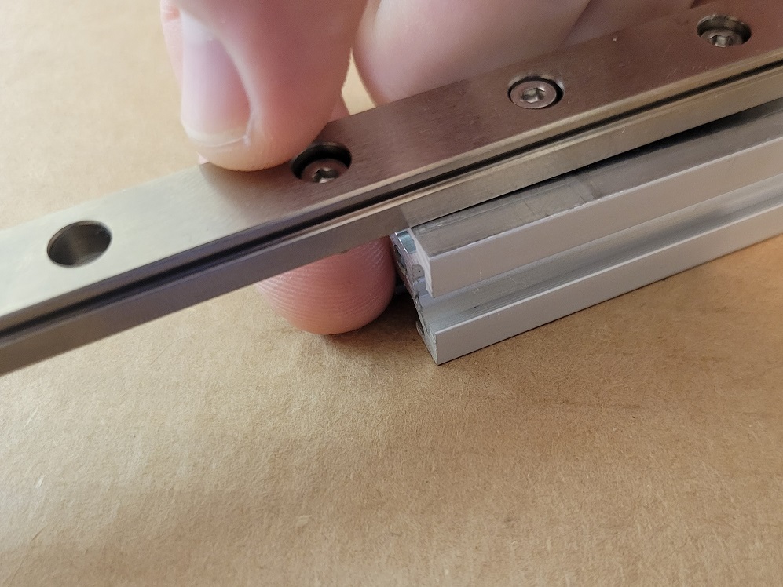
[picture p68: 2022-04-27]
docs/img/rail_install/oops1.jpg

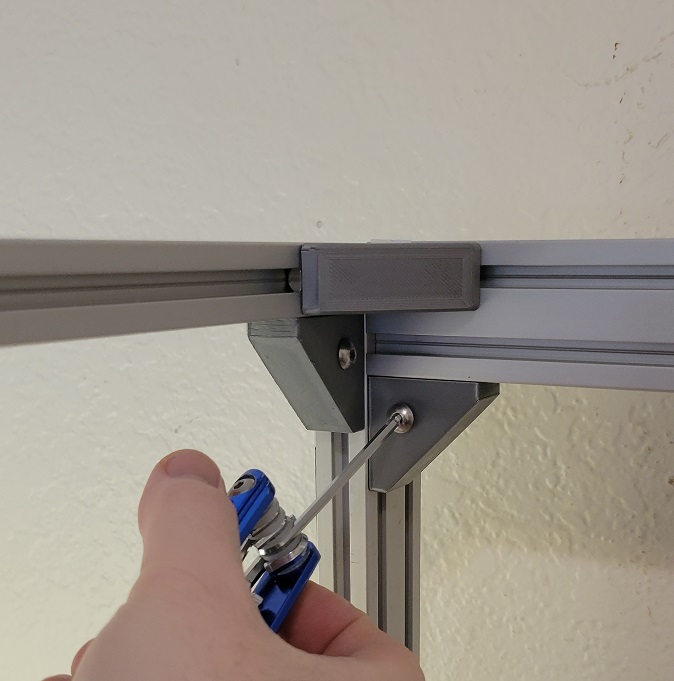
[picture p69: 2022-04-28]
docs/img/bracket_covers_center/step2.jpg

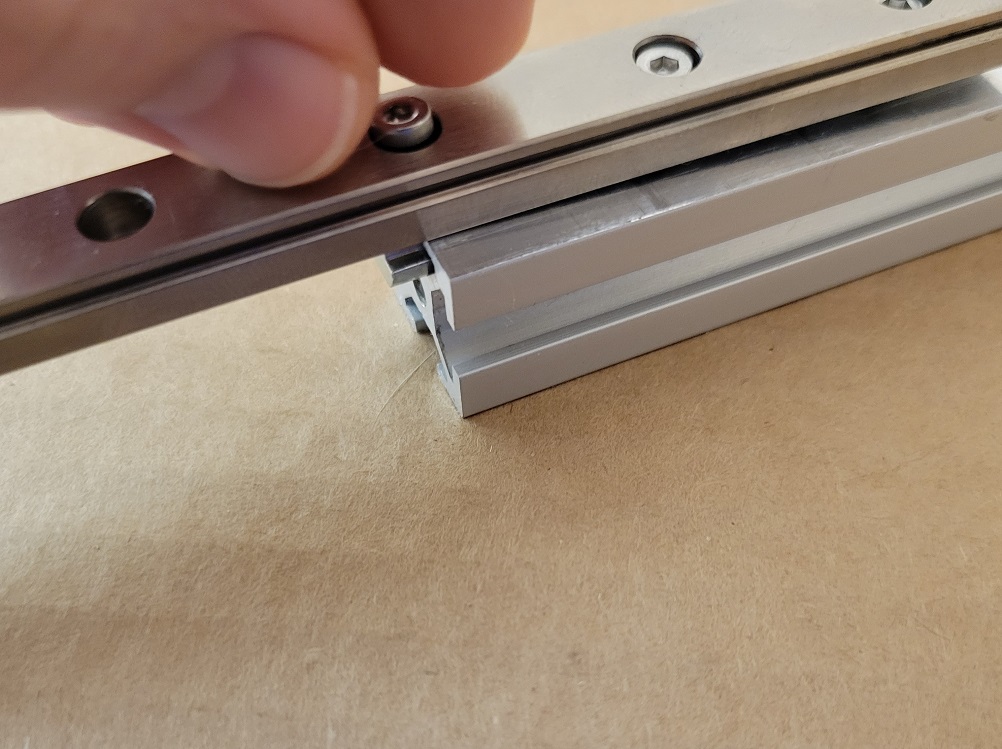
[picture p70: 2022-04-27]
docs/img/rail_install/oops3.jpg

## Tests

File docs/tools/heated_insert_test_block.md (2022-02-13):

# Heated Insert Parameter Testing Tool

## What to Print

You will need to do the test process twice, once printed flat and once vertically. The file needed is `M3 Het Set Insert Parameter Block.stl` file in the `/STL/Tools` subdirectory.

## Hole Sizes

Below are the sizes and taper angles of each position on the test block.

| Diameter | Taper 0 | Taper 1 | Taper 2 | Taper 3 | Taper 4 | Taper 5 |
| :---: | :---: | :---: | :---: | :---: | :---: | :---: |
| 4.35 | 0 | -2 | -4 |  X |  X |  X |
| 4.50 | 0 | -2 | -4 | -6 |  X |  X |
| 4.65 | 0 | -2 | -4 | -6 | -8 |  X |
| 4.80 | X | -2 | -4 | -6 | -8 | -10 |
| 4.95 | X |  X | -4 | -6 | -8 | -10 |

## Using the Test Blocks

Start with the top three insert holes. Press the inserts (preferably with a insert press) and note the characteristics:

1. How readily the insert drops in: is there resistance? Does it seems to just fall right in without grabbing the plastic? There should be some resistance, but too much will cause plastic to bubble up inside the threads.
2. The resulting plastic around the insert: does it raise at all above the insert? Is there a clear gap around the knurls? Is there a smooth transition between the plastic around the knurls and the untouched plastic? You're looking for the last of the three.
3. The bottom of the insert: is it smooth? Did any plastic seep up from underneath? Too high signals your insert is not fully seated. Too low is caused by plastic coming up underneath the insert.

Using the following three checks, move down and to the right, noting which insert "feels" right in each row (not too much pressure, not too little). If a taper of doesn't work for one row, don't re-use it for the next row. Keep moving down and to the right.

Your finished product should look something like [this picture](../Media/). Note that an insert was plucked out (with tweezers!) before being fully inserted. If you feel too much resistance with insertion or generally feel it's the wrong size, it probably is the wrong size.

Carefully look over the inserts and check depths with calipers. You're looking for the correct depth (5.8mm) and a smooth surface. In the picture, the ideal size wound up being 4.5 with a taper of -4 degrees (third row, third column).

## Updating the Fusion Model

The `Parameters` file will need to be updated. `M3_insert_dia` and `M3_insert_taper` are the respective parameters to set. From there you will need to update and export the STL files.

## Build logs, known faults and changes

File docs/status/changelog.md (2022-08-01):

---
title: Changelog
summary: Regular changelog of project changes.
authors: Jon Harper
date: 2022-06-05
---

This is a changelog for Clock 3, beginning August 2021 during the end of testing the previous version.

This page is built from source and may be stale. If you are viewing from the documentation site (jon-harper.github.io/clock-3), there may be more recent addtions [here on GitHub](https://github.com/jon-harper/clock-3/blob/main/docs/status/changelog.md) that have not yet been rendered and uploaded.

## Q3 2022

### 2022-07-02

- Development is slowing for the moment. I am in the process of possibly relocating.
- I am fairly certain I have a solution for the hotend wiring using a 16-pin Molex connector.
- Once the connectors arrive, the next step is to design a wiring box for it compact enough to fit near the hotend.

## Q2 2022
### 2022-06-19

- Documentation: Reworked the assembly index page.
- General: Added category/topic to changelog lines.

### 2022-06-18

- X Gantry: Adjusted the back mount and part fan mount to slide together more easily and prevent left/right deflection of the duct.
- X Gantry: Right side hotend screw mounts are now 19mm apart, suitable for mounting an Adafruit ADXL345 board.

### 2022-06-16

- Re-exported the X gantry carriage mount.
- Printing the new X gantry for Clock 3 *on* Clock 3.

### 2022-06-15

- ABL is functional after twisting the wires to reduce noise.
- Testing new hotend mount and panel mount ideas on an Ender 5.
- Pace of development is slowing now that the printer is mostly operational. Current remaining issues are:
    - Wire panel at toolhead
    - Z axis stability
    - Z axis clearance (filtration blocks lower half of movement)
- Tested print quality at 0.08mm and satisfied with results so far.

### 2022-06-11

- Modified hotend mount to be slightly taller and added mounting point for an accelerometer.
- Currently working on ABL configuration.
- Switched lights over to strips instead of the temporary main overhead lights.

### 2022-06-10

- Modified part cooling intake and back plate to allow heigh adjustment for the cooling fan.
- Reverted EVA duct to previous version to allow for the above to work.

### 2022-06-09

- Lots of refactoring for the new gantry/hotend. Most parts needed at least one reprint to fix minor issues.
- Assembled first full set of test prints. Part cooling fan will need work.

### 2022-06-08

- Gantry frame, hotend mount/cooling duct/etc., and part fan/part fan duct are finished.
- Still missing extruder mount and wiring panel mount for toolhead.
- Clock 3 is back up and running. Will need plentiful M3 lock washers. I suspected this, but learned the hard way.
- New X Gantry went through multiple print iterations. Having a second ABS printer (and a CoreXY one at that) helps greatly.
- Added a couple of renders of the new hotend and gantry.
- Still missing a wiring panel and the duct needs adjustment.

### 2022-06-06

- Tweaked latch designs somewhat for cleaner appearance and open/close action (PN129-PN131).
- Tweaked initial floor tab design (PN132), twice. Smaller and actually fits!
- Continuing to evolve ideas for hotend/extruder/part fan mount.
- Relocated a number of doc files for better access to info from the landing page.

### 2022-06-04

- Added feet resolved stability issues, though a more stable surface would still help.
- *Printing both ABS and PLA today*.
- Started work on a new hotend/gantry carriage format. Still deciding best directions, however:
    - Footprint is narrower
    - Ducting is much tigher to the heatsink on the X axis to help with directed cooling;
    - Hotend cage is 6mm shorter on Y axis, as well
- Still early on designing this, so it'll be awhile before I find a good combination of component mounting methods and arrangement.

### 2022-06-03

- Added PN131, a lower door latch.
- Also working on PN132, a spinning latch for the floor panels.
- Gasketing went in perfectly. Clock 3 is sealed.

### 2022-06-01

- Fixed Z axis issue—the anti-backlash nut wasn't secured properly on Z2.
- Printing successfully today.

### 2022-05-31

- Modified the door latch for wider opening arc.
- Testing TPU door seals and gaskets. Currently testing TPU with E6000 glue and have Loctite 406 on order.

### 2022-05-30

- Fixed numerous kinematic values for steppers. XYZE are all calibrated now.
- Made a custom temp map for the thermistor I'm using.
- Stability issues. Not sure if bed or gantry.
- Added PN129 and PN130 for a front door latch.

### 2022-05-29

- RGB lights do not work, possibly because of the SP901E. I have replaced these with 12V white LEDs for now.
- Chamber is sealed except for the around the flooring edges. May another gasketing material.
- Hotend thermistor is inaccurate. Going to create a resistance table.
- Door and all panels are back on.
- Kinematics work.
- Fans for both chamber and electronics are configured and working.

### 2022-05-28

- Undercarriage wiring is in with no issue.
- Chamber is now sealed except for:
    - Door gasketing
    - Side panel weatherseal
    - Wiring tunnels (left and right)
- New panel mount works nicely.

### 2022-05-27

- Finishing up the first electronics section and wiring details.
- Steppers mount on the panels with no issue.
- Side panels work, although initial mounting of the couplers is tough.
- Switching to final color scheme; looking good.

### 2022-05-21/22

- Panel mount can be adapted and will be.
- Have already pushed changes to hotend for BLTouch mount points; will add BLTouch adapter later after testing.
- Z Axis assembly largely finished; outline done for Z Axis section of the documentation.
- Mostly done with XY axes outline.

### 2022-05-12

- Had some catastrophic issues with multiple SKR 2s. Had to switch over to Octopus 1.1s, which required a new control case. That took a week.
- I have two printers up and expect to have a third printing ABS by tomorrow.
- Testing with Clock 3 hotend cooling assembly and BMG on an Ender 5 is going extremely well.
- Also testing a hotend panel mount on an Ender 5.
- BLTouch will need some work, so opened issue #50.

### 2022-04-27

- Still working on documentation. I took a week off to solve some long-term issues and test out a few things.
- Documentation is now merged into the clock-3 repo instead of being its own repo. This will simplify a lot of things.

### 2022-04-17

- Doing a lot of experimentation and testing right now, as well as catching up on maintenance.
- Focus ATM is testing the hotend & related assemblies on an Ender 5, including a new wiring panel mount. Will adapt for Clock 3 afteward.

### 2022-04-14

- Making heavy progress documenting assembly.
- Panels are finished, insulation is 80% done.
- Made a number of model fixes based on assembly experience, all related to fasteners.

### 2022-04-11

- Finished testing Micro Fit 3 profile, updated PN070
- Fixed #45
### 2022-04-08

- Made some milestone changes. See below.
- Adjusted due date for 0.4.5 (pre-assembly testing).
  - Although the Micro Fit 3 profile is done, it's not tested.
  - The BOM needs to be broken out into the Sales BOM and the Manufacturing/Assembly BOM. This (kinda) exists with the Materials/Parts sections, but they are different things and need to be broken out.
- Documentation is progressing steadily in parallel, but can't progress while the BOM is changing (i.e. reference points might change).

### 2022-04-07

- Today is yesterday on repeat, but with more progress.
- [jon-harper.github.io/clock3-docs/](https://jon-harper.github.io/clock3-docs/) is live, if incomplete.

### 2022-04-06
- Continuing to flesh out the documentation basics
- Started sealing the panels with polyurethane.

### 2022-04-05

- Filling out docs in earnest now.
- Rigid coupler link in the part list/BOM is now correct
- Documentation changes are now tracked in the documentation repository.
### 2022-04-04

- BomDialog now exports both CSV and Markdown formats.
- Panels are sanded and ready for better weather to apply PUR.
- Pushed first working BOM exporter with Markdown support.
- Documentation framework is progressing steadily.
- Created a panel mount profile for the MicroFit 3.0 dual row, two pin connector.
- Earth wire is now 16awg.
- Lots of added links and corrections in the part list.
- Updated `/Scripts` readme text.

### 2022-04-03

- Apparently never exported PN127 and 128, the TPU wire conduits. This is fixed.
- Continued prepping panels for sanding and sealing
- Significant progress on BOM export as a Markdown file.

### 2022-04-02

- Setup `clock3-docs` repository and MkDocs.
- Started work on a new script to re-format the `BomDialog` output CSV file into Markdown. This will possibly make its way directly into Clock3Scripts, but it's useful enough to leave it in the `/Scripts` folder.
- Spent much of the morning setting up to seal the panels in polyurethane. 

### 2022-04-01

- Assembled exterior frame, planned assembly order.
- Checked panels for fit.
- Removed extrusion channel guide from frame feet. This should greatly speed up the print time and reduce supports.
- Re-ordered Micro-Fit 3.0 panel mount connectors. USPS mis-delivered my package.
- Will likely use Jekyll for docs.
- Found the missing tee nut. BOM and model are now fully in sync and verified.
- Relabeled all extrusions with cleaner labeling

## Q1 2022

### 2022-03-30

- Added more layout files for exporting STLs
- Exploring documentation formats
- Picked up completed panels (YES!)
- Began "pre-assembly" of frame

### 2022-03-29

- Export BOM dialog works (mostly). Pushed an update to Clock3Scripts.
- Exported a working, auto-exported bill of materials.
- Removed old scripts folder and put in placeholder.
- Firmware folder is now just a `readme.md` with information on where to find the Klipper config and such.

### 2022-03-28

- Added a new repository for the Fusion scripts: Clock3Scripts.
- Migrated old scripting issues to Clock3Scripts.
- Added new linear rail alignment tools for during assembly.

### 2022-03-27

- Added a printed number to PN033, the front mount plate.
- Two new renders of the model with final panels.
- Verified all printed part counts and heat set inserts against BOM.
- Tested LED mount length.
- I believe the BOM is correct with respect to Micro Fit 3.0 connectors, although the panel mount parts are not here yet.

### 2022-03-26

- There is a literal, phantom tee nut in the model. I have counted component by component three different ways. The's an extra tee nut hidden in the model. =(
- In the process of counting, `Connectors.xlsx` is taking on new responsibilities, i.e. it's now named `ID Lists.xlsx` and contains information on parts that require fabrication or assembly: frame + tee nuts, printed parts + heat set inserts, and all of the cables.

### 2022-03-25

- `Frame Identification.pdf` now has handy arrows to the front, top left corner of each piece and an explanation of the labeling system.
- Switched hotend wiring to 20awg and connector to Micro Fit 3.
- Fixed #42 (A/B steppers have pigtailed connectors now)
- Chasing a phantom tee nut.

### 2022-03-24

- Created a set of drawings to identify and label frame components
- Spent most of the day locating and counting M5 roll in tee nuts.

### 2022-03-23
- Fixed #39 in the model.
- Fixed #35. Reprinting.
- Added more wire anchors to the model.
- Added a subfolder in `/CAD` called `Font`. Inside is Hack, the monospace font used for labeling part numbers. A readme and links to the project page are included.
- Fixed #41 by modeling the USB C buck converter.
- Started a Fusion plugin to collect scripts.
- Fixed #38.

### 2022-03-22

- Opened a lot of issues and a new milestone.
- New render.
- Nearly all components are counted from the BOM.
- Set side panel depth to 6mm to fit all panels on 1x 4'x5'x12mm sheet and 1x 4'x5'x6mm sheet.
- Will need to rework acrylic to 3mm. 6mm total with an air gap is sufficient. This was pointed out by the fabricator (thank you, Michael).
- Finalized laser cut layout and submitted for fabrication.
- Started modeling PTFE filament guide.

### 2022-03-21

- Integrating printed parts to general part list.
- Parts have new, simpler name scheme and .stl filenames are auto-generated. Now to update the model...
- New PN070-073 (electrical panel mounts).
- Removed panel mount frames, PN074 and PN075.
- Renamed STL files to match new naming scheme.
- Inserted panel mounts into the model.
- Added PIR foam cutouts for panel mounts, which were previously missing. Have not updated drawings yet.
- Updated each component in the model with new Description fields and checked for issues.
- Fixed #31. PSU now uses M4x8mm BHCS.
- Uploading an initial, mostly verified, bill of materials.
- Fixed depth of external couplers on the side panels.

### 2022-03-20

- Working on issue #28 fairly steadily.
- All wire runs will now have an ID to aid tracking and assembly.
- Wire IDs are based on component IDs
- IDs not involving the PSU are tailed with a letter code indicating distance from MCU, e.g. HE-A is MCU->chamber panel mount, HE-B is from the right chamber panel to the tooldhead panel.
- There are a few third level connectors with a -C. The modified BLTouch wire is ABL-C and connects to ABL-B. Likewise, I included a -C for LED strips. Even though they are soldered on, they still have to be made by the builder. 
- Added initial drawings for foam insulation to the `/BOM` folder
- Tallied and labeled all wires, connectors, and pins.
- Updated ExtractBOM_PN. File location is currently hardcoded and it lacks a UI, but those are already on the radar.

### 2022-03-19

- Adjusted dimensions to be uniform 6 or 12mm for panels due to material availability.
- Updated model and laser cut sketches.
- Working on a new panel mount design.

### 2022-03-18

- Laid out panels for laser cutting on 4'x5' sheets.
- Now have both engineering sketches and laser cut paths in the `BOM` folder; closing #33

### 2022-03-17

- Finished draft of engineering sketches.
- Several more renders of the panels for the fabricator to see.
- Re-export PN016, the stepper mounts, as I forgot on the 16th.

### 2022-03-16

- Completely remodeled the outside frame and panels, as the timeline was already in bad shape. It finally got corrupted and I threw it out and started over. The results are much cleaner.
- AB stepper mounts are 5mm shorter (again).
- Restarting engineering sketches again due to frame and panel problems. Should go much more quickly.

### 2022-03-15

- Modeled piano hinge
- Attempted to update the the `Outside Frame` file and on to finish the drawings, but Fusion is crashing constantly.
- Will need to merge printed part list in to `General Part List.xlsx` for proper export as a CSV.
- Exported first completed set of panel sketches.

### 2022-03-14

- Cleanup and tweaking to the readme file.
- Lots of issue and milestone cleanups.
- Preparing `General Part List.xlsx` to be exported as a `.csv` file instead of tab-delimited.
- Will need to merge printed part list into the general file.
- Added a value column and merged the default values.
- The Fusion Python script now reads in the CSV file and optionally includes default values, then scrapes the model for part numbers, and exports to a specified file.
- The UI does not work correctly. It appears, but events do not fire properly.

### 2022-03-12

- Added printed part numbers to PN123 and PN124
- Minor edits and updates to the `General Parts List`.

### 2022-03-11

- Picked up on learning Fusion's UI API. It's built on Qt, so very familiar.

### 2022-03-10

- Learned a few lessons and laid out the panels as derived objects in a separate file, then created the drawings from that.
- Waiting on a piano hinge to draw up the top panel and hatch.
- All other fabricated pieces have drawings now.
- Exported the initial sketches (minus the top) to the `/BOM` folder.

### 2022-03-09

- Top hatch is now 300mm deep instead of 390. This leaves room for a spool holder on top of the printer.
- Continuing to work on drawings.
- Multiple new renders to illustrate paneling.

### 2022-03-08

- Exported initial designs for panels and a mockup of panels/frame to discuss with fabricator.
- Began engineering drawings for panels.

### 2022-03-06

- Finished disassembling frame.
- Modified base foot design to accomodate roll-in tee nuts.
- Now verifying total on hand count against the model.
- Aside from count verification, BOM just needs connector count and cable lengths.
- Closed disassembly milestone.

### 2022-03-05

- Re-exported PN099. File somehow got lost without being replaced.
- More fastener length fixes.

### 2022-03-04

- Continuing model and BOM verification. Working on kinematic components today.
- Restored PN088, the camera base.
- Added a linear rail plug that can be printed in TPU in case they are lost (I need them right now; figured they can't hurt).
- Lot of corrections to fastener sizes.

### 2022-03-03

- Continued model/BOM verification.
- Lots of fastener adjustments, but no major surprises
- The electrical panel mount will definitely need redesign, and the PSU mount is dubious.
- Also need a mount for the new RPi buck converter.

### 2022-03-02

- Began verification of BOM and model.
- Replaced M5x12 SHCS for the doors with M5x16.
- Shortened air filter base stand top 2mm.

### 2022-03-01

- Moved exhaust hose and PTFE coupler exits. Panels are no longer identical but this is much simpler to work around.
- FPD of wire conduit for the paneling. Since there is no physical paneling yet, the conduit will definitely need revision later. This is mostly to ensure it's doable, counted in the BOM, and have *something* to test when the paneling is fabricated.
- Model is now missing only lock collars for the F688 alignment bearings.
- Only remaining design necessary for a complete prototype are TPU gaskets for the front door. Changes definitely need to be made around the hotend and (later) the Z axis, but an enclosed prototype is almost here.
- BOM is accurately generated for all **printed** parts but lock collars and some extra zip tie anchors.
- Added the aluminum facing for PIR foam, fixed numerous issues.
- Several new renders.
- Added quite a few zip tie anchors to the model, as well.
- Added foam weather stripping to the sides of the floor panels.

### 2022-02-28

- Massive number of small edits to filenames, `Printed Part List.xlsx` and model to ensure consistency.
- Updated Raspberry Pi in the model, adding heatsink, HDMI adapter, and SD card.
- Removed even more stale STL files.
- Added PN111, a fan finger guard with about the right amount of spacing for a M3x35mm screw.
- Added SD cards, thumb screws, and other small details to the models.
- Updated the Readme file with my spare time while Fusion saves.
- Designed two styles of pull handles: one is narrow to fit the V-slot door, the other is 25mm wide for everywhere else. PN125 and 126
- Started work on wire pass-thrus for the flooring.

### 2022-02-27

- Removing PN095 and 097, as the panels are done and no M5 inserts were needed.
- Renumbered PN089 to PN095. It's now circular and is used on all A/B and Z steppers for a near-airtight seal.
- Added PN123 and PN124, the bearing slider mounts for the Z axis (left and right).
- All printed part file names have three-digit numbers now, e.g. `090 - Misc - Frame - Corner Bracket Cover.stl`. This will help sorting on every platform other than Windows.
- `Printed Part List.xlsx` is updated to reflect three-digit file names, as well.
- Added PN122, a PTFE tube guide for between the pneumatic connectors for PN120
- Fixed outside panel coupler dimensions for new panel widths.
- Moved some brackets slightly to work with thicker floor panel.
- Modeled all remaining insulation and added relevant parts.
- Finished adding fasteners to the floor panels.
- Working on ensuring the air filtration both fits and can exhaust easily. This may require work, but is doable.

### 2022-02-26

- Set panel thickness to 7/32" or ~5.56mm for front panel.
- Side panels and top are now 5/16".
- Rear panel and flooring is 7/16".
Updating model positions and sketches.
- Deleted STL files for SKR board mount, as the board itself is currently unsupported.
- Running hard against physical memory limits with Fusion when loading the master model. Pagefiles are still on spinning disks on my machine, not flash, so pagefile thrashing hurts and is possibly causing crashes.
- Fixed the alignment of a few brackets.
- Floor panel dimensions are in. Still finishing adding insulation and fasteners.

### 2022-02-25

- Lots of part corrections in the model.
- Modeled and added the 3mm spring steel build plate.
- Finished the front door and related components in the model. Added M5x14 FHCS to the BOM.
- Cleaned up the frame components to be external references instead of internal. Will fix the XY and rest of Z axis tomorrow.
- PTFE coupler and hose exhaust work well--will need TPU guide between the pneumatic couplers to align the PTFE tubes.
- Readme edits.
- Two new renders added.

### 2022-02-24

- Assembled and measured door. Approximate clearance with MISUMI hinges is 4-5mm on the handle side.
- FPD of hose exhaust and PTFE coupler for side panels. Adding PN120 and PN121.
- Testing stability of door. I've mocked up spacers that are as thick as the paneling, but I believe they are allowing the door to sag.
- Modified PN092, the frame base foot, to work with BHCS.
- Corrected a few file names against the master log.

### 2022-02-23

- Modified AB stepper mounts and TPU shim to sit on top panel.
- Extended AB stepper mount height, now uses M5 x 60mm BHCS.
- Added PN089, a stepper alignment slider. It's a TPU plug for where the linear rods from the AB steppers enter the top panel. A ball bearing sits in it and plugs the bottom to keep it airtight, but the top has room for the bearing to slide sideways to get it precisely positioned.
- Added some lateral clearance for the stepper mounting holes, as well.
- Removed `AB Stepper Modules` from the `XY Master` and pulled it into the `Master` file because it mounts above the enclosure.
- BOM tweaks.

### 2022-02-22

- Adjusted PN083/PN084 clearances around the extrusion.
- Tweaking master part list entries a bit, adding "Supplies" category that includes items of indeterminate quantity (e.g. lubricant) or that may be on hand as a tool (e.g. screwdrivers) and generally don't go on a BOM but will be needed.
- Removed old PN082 file.
- Rebalanced screws on the Z Gantries. There are now three M5 on top, three under.
- Finished insulation and fasteners for all of the panels but the flooring.
- Updated the master model and removed old paneling.
- Added in feet to the `Outer Frame` model.

### 2022-02-21

- PN100 is finished. PTFE tube stays neatly out of the way and has a shorter feed path.
- Adding new milestones and issues to help sort short- and long-term goals.
- Turns out PN083 and PN084's issues are not thickness underneath the insert but severe ringing by the printer. Removed the issue. Will fix belt tension on printer later.
- Adding insulation and joints to the new panel models in the Outer Frame file.
- Finishing out the connector list based on the wire harnesses.

### 2022-02-20

- Iterating through PN100 to get a satisfactory design.
- Nearly all internal connector wires have a prespecified length now. I will leave the undercarriage unspecified as it's short enough it can be left to the end user. Plus no two people are going to want to arrange it the same way.
- Not a lot of model progress today; focused on wiring.
- Now using a PTFE tube to stiffen the hotend wiring loom. No filament is in it--it just adds rigidity.

### 2022-02-19

- Focusing on wiring today.
- `Connectors.xlsx` has a new tab for "Upper Level Wiring". This is wiring from the lower level patch panel up, e.g. to the hotend fans. Every connector has a pin count, recommended wire gauge, and approximate length needed. More will be filled in during disassembly.
- Added PN100, a PTFE tube guide to keep it from snagging the belts. The tube will now exit out of the back right, passing near the rear belts on the way. This will keep it out of the way and anchor it while the hotend moves.
- Top panel and hatch are modeled with a piano hinge.

### 2022-02-18

- Added twin cutouts to the side panels. Right side cutout is for PTFE conduit, the left side is for exhaust.
- Still considering approachs to wiring for the hotend.

### 2022-02-17

- One year since this all really started in earnest.
- Uploaded parametric t-slot extension for the electrical undercarriage, closing #14.
- Installed thermistor for the electronics (`TE`).
- Updated `Connectors.xlsx` to reflect minor changes.
- PN013, Tensioner Cap: fixed issue with impossible to print features. M5x25 instead of M5x16 screws are needed. They're already needed for the tensioner bolt iself, so no new fasteners are introduced.

### 2022-02-16

- Raspberry Pi board mounts (PN083, PN084) are now horizontal to allow better airflow, fixing #15
- Part numbers are now broken out into "General Part List" and "Printed Part List"
- All part numbers are now three digit.
- Created wire anchor assembly.
- Door frame assembly is modeled, minus the hinges.
- Concerned hinge gap is too small for door frame, or may leave too large a gap on the handle side. May need to design printable hinges to properly align.

### 2022-02-15

- Fixed a ton of minor issues with brackets in the model.
- All brackets are now properly positioned and should be propogated.
- Removed brackets from the bed frame; will rely solely on printed parts.
- Bracket assemblies still used SHCS instead of button head; fixed and propagated.
- Filtration is in the model.
- Finished renaming printed part numbers.
- SP901E has a placeholder body with fasteners in the model, temporarily addressing #21.

### 2022-02-14

- Fixed outer frame for part ID purposes.
- Added invisible SP901E assembly to the model to get it and the appropriate fasteners inventoried.
- Updated base foot and LED strips for part numbers.
- Too many minor changes to count.
- Lots of work on the prototype to reassemble the fixed skirt panels.

### 2022-02-13

- Temporarily removed the part codes Markdown file, as it is not current. Too many changes are taking place with the BOM to keep up.
- Renamed `Printer Part Codes.xlsx` to `Part Codes.xlsx` and shifted it to the `/BOM` folder.
- Replaced stock nuts with anti-backlash in the model, fixed some missing screws in the `Z Master`
- Adjusted RPi panel mount connector profiles. The skirt is now fully modeled and should be correct in the BOM. Also tested and working.
- Made exhaust adapter fully parametric and exported to `/CAD/Templates` folder.
- Ditto LED Guide Channel.
- Exhaust adapter now has a larger fan exhaust duct coverage area to help keep it in place.
- Mass renamed filtration parts with appropriate names and updated `Part Codes`.
- Finalized Vertical Filter model.

### 2022-02-12

- Exported parametric tools for heated inserts.
- Changed a few part categories and added a "Type" column for parts.
- Modified the 80mm fan grill for better printing.
- I believe all but some very odds-and-ends parts have numbers, so closing issue #20.

### 2022-02-11

- Tensioner definitely needs rework.
- Removed PN100-PN103, the frame caps. With wood paneling, they are unnecessary.
- Pushing the `ExtractBOM_PN` Fusion script.
- Re-exporting files and continuing reprints before disassembly.
- Added a lot of entries that are not modeled, like heat shrink and zip ties.
- Most entries in the parts list now have links to reference suppliers
- New 80mm fan mounts for front and rear panels, with PNs 102 and 103

### 2022-02-10

- Continuing fresh reprints. May have discovered an issue with the tensioner.
- Adding reference links to the BOM.
- Most parts are now in the BOM--looking to address issues like zip ties and other oddments
- Considering using placeholder (empty) bodies with part numbers to trigger the script when scraping for BOM.

### 2022-02-09

- Moving through components to add part numbers and locate model inconsistencies.
- Resolved some very old model components that didn't get updated against the prototype.
- `Printer Pard Codes.xlsx` has a significant update with tabs for each BOM category.
- Fusion model now is largely updated with internal part codes for auto-generating a BOM.
- Python script for scraping part numbers and instances is initially done.
- Removed a lot of unused and outdated files from the Fusion project.
- Removed PN080 and PN081, the freestanding 80mm fan mount and grille, along with some other stale entries.
- Exported XY Pulleys and XY Joints again for final reprint before disassembly.

### 2022-02-08

- Lots of progress auto-generating a BOM, though I will need to individually tag each part that needs to be included.
- Each part is tagged with a part number starting in "PN". These match up with the printed IDs, but are extended to any BOM part.
- This should massively speed up generating the BOM, as there are fewer parts added to the list (the script doesn't add anything without a "PN" part number).

### 2022-02-07

- Visual display of chamber temperatures is critical, so I'm quickly adjusting the default display for Klipper.
- I also plan to change the menu layout, so I'm laying the groundwork for that, as well.
- Created a repository for [Clock Face](https://github.com/jon-harper/clock-face), as I'm calling the display screen.
- Removed the OctoPrint menu and changed "SD Card" to read "Virtual SD"
- It works and I've sketched up a new menu layout, so stopping on that for now.

### 2022-02-06

- Updating issues.
- Going with a very simple, conservative, notched-edged panel approach for the floor.
- Working on auto-generating a BOM

### 2022-02-05

- Closed #11 regarding air filtration, as a working vertical prototype is completed.
- Will proceed with 0.2" plywood for panels due to cost.
- FPD of a new gantry lock bar.
- All project files now up to date with parametric heated insert holes.
- Enclosure maintaining at 45C with 48C target

### 2022-02-04

- Enclosure maintains 3C above target at 45C.
- A 2/3 full 75mm tank is currently doing the job. Printed off two 50mm tanks.

### 2022-02-03

- Working on testing Klipper, lights, and the exhaust in an enclosure.

### 2022-02-02

- Modified exhaust adapter for ~20mm OD hose.
- Continuing to work on enclosure/Klipper/filtration integration
- Widened HEPA filter latch for vertical filter.
- Added a render of the finished filter assembly.
- Added pinout diagram for the SKR 2.

### 2022-01-25 - 2022-02-01

Focused at the moment on finding a plastics fabricator to answer some basic questions about material and panels.

Meanwhile, since I can't enclose the prototype yet, I've setup Klipper on the ABS printer and am getting that ironed out. This way I can test the chamber exhaust in an real-world environment.

## Q1 2022

### 2022-01-24

- Tested filtration with 75mm fans; much improved.
- Fit tested model with shroud--may need some minor adjustments to maintain tension around the HEPA filter.
- Current cold temperatures are making it diffiult to maintain chamber temps, so having more warp than usual and therefore more reprints.

### 2022-01-23

- Tested the filtration; seems to work slowly but efficiently. Likely will rely on 75mm fan solution.
- Iterated through some changes to the base and fan intake for the vertical stand.
- Added a shroud to help keep the HEPA cartridge in place
- Modified the TPU latch to print on its back.
- Found two Raspberry Pis.

### 2022-01-22

Filtration

- Added a small hole to the center of the 75mm tank to add more perimeters for sturdiness. The center pillar is pretty weak.
- AC -> HEPA duct is done for the vertical filtration assembly.
- Testing dual 50mm fan setup in an enclosure today.

GitHub

- Added a number of issues to GitHub and pinned an issue containing a list of what needs closing before disassembly.
- Removed Marlin firmware folder. It's not maintained or even finished, nor do I intend to move away from Klipper now.
- Reworded some of the readme.md and slimmed it down. Moved the TODO entirely to Issues.
- Moved orientation-specific STLs for filtration to subfolders.

### 2022-01-21

Clock 3

- Renaming a lot of the components to group them by function.
- Added a new #95: a panel mount piece. A 50 pack of M5 heated inserts is $14 and will cover any panel subdivisions I need to make, as well as possibly being useful elsewhere.

Filtration

- Made shims/TPU gaskets for both 75mm and 50mm fans. They push the fans out 1.6mm to make room for a hose adapter (and dampen noise).
- Both the 50mm and 75mm fan intakes work, though the right 50mm profile is incorrect.
- Working on 75mm fan exhaust to tighten fit. Modeling is difficult as there is some variation between brands in wall thicknesses, etc.
- Ordered 1" ID hose instead of 1/4". The 75mm fan is having difficulty providing pressure, so I'm going to try avoiding necking down. The 1/4" hosing may still be useful for 50mm fans.
- 1/4" hose is ideal for 50mm fan.
- 50mm fan intake is now front heavy with hose on, added hole for an insert and foot.
- Started work on a fully vertical filter tower.

### 2022-01-20

- Will need TPU shims to leave room for tubing connectors.
- Fixed fan holes to fit regardless of orientation.
- Added foot to 75mm fan intake.
- Added small front foot to use with 75mm fan intake
- Modeled 75mm radial fan

### 2022-01-19

- Dual 50mm seem like they would work for a small chamber, particularly with one 50mm running continuously as exhaust.
- Modeled and started a FPD for dual 75mm blowers.
- Looking into flexible hosing, ordered 1/4" ID, 1/2" OD silicone tubing and push connectors.
- Dual 75mm is front-heavy.

### 2022-01-18

- Created a hole diameter test for heat pressing with variable tapers.
- Big change in standard heated inserts after testing. All inserts (both vertically and horizontally) will default to 4.5mm with a -4 degree taper.
- Re-exported all affected STL files.
- Created `heated_insert_test_block.md` in the `/Docs` folder to explain heated insert testing.
- Air filter prototype is finished; waiting on new fans to test.

### 2022-01-17

- Filtration: Finished the latch, hinge, and carbon tank gasket.
- Added in all fasteners to the filtration model.
- Started printing FPD of components.
- Added renders to GitHub.
- Hinges work, latches align.
- Remodeled backside of activated carbon duct to reduce weight by 50 grams, down from over 200 (2mm perimeters, 20% infill).
- Generic ABS not happy with such a large solid volume (delaminating). Printing in PETG for now, will switch to modified ABS later.

### 2022-01-16

- Took a break yesterday; came up with some good ideas.
- ~~Working on a relatively straightforward, 3-fan filtration setup, but need to dissect a fan first to get the diameter of the inner bearings.~~
- Destroyed a fan; starting over.
- Almost done with a different setup using just two 5015 or 7530 fans.

### 2022-01-15

- Activated carbon appears to be a good supplier. No sign of rust on any of the test items.
- Updated the FAQ a bit.

### 2022-01-14

- Waiting on HEPA filters so working on polishing XY components for milestone print.
- Added surface chamfers to XY Pulleys, XY Joint components.
- Fixed #1 and #2 ID text to specify that they are Left side components.
- Redid #8, R Top XY Joint. Center rib now stretches to the wire anchor, the anchor is slightly deeper, and there is now a lip around the rear edge.
- Found a screw hole that somehow got lost on #10.

### 2022-01-13

- Had some initial success using a French press filter to hold the activated carbon.
- Testing a lid with another French press filter to act as a sealed container for activated carbon.
- AC will either need to be pre-sieved or thoroughly shaken in the container to sieve the finer particles out.
- Last export of bed corner bracket didn't have part code. This is fixed.
- Modest edits to the readme.

### 2022-01-12

- Working on some concepts for filtration.

### 2022-01-11

- Fixed mounting hole size for part cooling fan.
- Created a skeleton FAQ.
- Added a note in the `/Firmware/Klipper` folder where to find the `.cfg` files for Klipper.
- Testing virgin coconut shell activated carbon for oxidation. Hopefully this is a good supplier.
- Raised A/B steppers a few mm. Now use M5x45mm screws.
- Lots of issues resolved on the X Gantry and hotend.
- Changed mointing direction for part cooling fan. Heated insert no longer enters at an angle, which should help alignment issues.
- BLTouch mount works.
- Pretty much every component touched to update `Parameters` file. No changes due to new parameters yet.
- Went through a number of iterations on the camera mount. Have settled on a location near the front left on top of the tensioner.
- Steadily adding issues to the issue tracker. Working on setting some initial milestones.

### 2022-01-10

- Hotend now locks in place with two screws into the mount itself, rather than passing through to the front plate. This allows preassembly of the hotend and fewer screws to remove the mount plate for belt access (4->2).
- Between the above and changing the fan screws, the hotend cage, fan and all, can be removed with 4 total screws instead of 8.
- Fixed an issue with the front mount plate's vent not passing all the way through.
- Steadily adding 0.4mm chamfers to narrow holes (mostly screw holes) that touch the build surface in case of elephant's foot. Completed hotend and stepper mount modification so far.
- Also moving ID # off the build surface if an alternate location is available, e.g. under the stepper on the BMG mount. This keeps the # from fusing closed.
- Added Octopus pinout diagram to docs.
- Belt clamps now have a 'U' shape with much more grip.
- Display works on prototype now. Note: Klipper docs use a reversed orientation for their board aliases from Marlin, so I skipped using aliases and directly inserted pins.

### 2022-01-09

- Created a Klipper config repository.
- Working on an Raspberry Pi camera mount.

### 2022-01-08

- Added #110 (a different #110), which is a panel mount for an SD card extension PCB. Crack the extension case, slip the cable through the back and the PCB into the slot. Mounts with 2 brass inserts.
- Finished prototype wiring, labeling, and front panel. Now working on Klipper.
- Need to flip RPi mount to lay flat for cooling.
- Started adding issues to Github.
- Working on initial Klipper config.

### 2022-01-07

- Printing was delayed by layer shifting on the 92mm fan mount. 
- Did a relayout on the left panel mount. The Fusion timeline is more manageable and the layout of the connectors more logical.
- Front panel mounts all fit save for Ethernet and SD Card--expect those to arrive today.
- Added zip tie anchors to the forward-facing side of the panel mount.
- RJ-45 cutout is off by a bit, but it fit after some effort. Going on the TODO list.

### 2022-01-06

- More wire anchors, more wire routing.
- Finishing front panel component printing.
- Added through hole for a screw to the display slot so that the front panel will have two vertical fasteners.
- Added a cutout for full size SD card slot with the rest of the panel mounts in front. Waiting on extension PCB to arrive in the mail, so no corresponding mount yet.
- Moved USB, HDMI, and Ethernet panel mounts to left panel to avoid crowding the display area.
- Modified left interior panel mount for chamber thermistor and chamber fan ports.
- Shortened and recrimped much of the undercarriage.
- Feeling more comfortable with the general state and layout of the undercarriage wiring.
- Shortened tops of wiring panel mounts to leave space for flooring panel to inset.

### 2022-01-05

- Working on wiring in general:
- Raspberry Pi now has a dedicated power/IO cable that I've hot-glued in place. I can't figure another way to properly secure Dupont connectors, as they don't latch. Hot glue it is.
- Created a harness to properly wire the SP901E and mounted it.
- Checked light wiring connections and recrimped a few.
- Added wire anchors in numerous locations.

### 2022-01-04

- Added JST SM connectors for the alpha and beta steppers. They now plug in to the back skirt end panels instead of being wired to the board directly. This modified #106 and #107.
- Designed skirt slot for display and USB, HDMI, and Ethernet ports.
- Started initial Raspberry Pi and Klipper setup.
- Reorganized fan headers, added Supply Voltage column to `Connectors.xlsx`.
- Finished the back skirt assembly, including today's modifications.

### 2022-01-03

- Added tab with a screw hole for the skirt grille. It's a little flimsy in the center currently.
- Modified power switch port to accept 15mm hex nut cutout. Should stabilize the power switch.
- Skirt ends: moved M5 hole down to give easier access with plugs and switches and such installed.

### 2022-01-02

- Tweaked frame caps so the screw holes are more printable
- Re-exported X gantry's front plate.

### 2022-01-01

- Back in office. 31 parts to print until I'm caught up.
- Strengthened PSU bracket
- Switched to M4 screws for PSU bracket (oops)
- Modified fan exhaust and intakes to print properly. Fan mount had impossible overhangs; this is fixed.
- Tweaked tolerance for IEC plug

## Q4 2021

### 2021-12-30

- Added some bracing to the electrical panel mounts to reduce flex and moved them further back.
- Introduced the wiring panels to the master model.
- Added lighting into the model for 3 x 12 pixel strips at 60px/m (16.6mm spacing).
- Made a few fixes to the lighting strip so the zip tie does not cross over an LED.
- Plenty of new renders.

### 2021-12-29

- Fixed ABL mount issues with belt attachment screws.
- Also simplified mounting the hotend fan. Two screws mount into the fan shroud and two pass through to mount both. The fan shroud and fan then can come off with two screws instead of four.
- Added motion joints.
- Reviewed assemblies and added any missing fasteners.
- Updated wiring anchors on the x gantry. BMG mount now has a groove and zip tie channels for wiring on the right side.
- `Electrical T Slot Extension` now has a slot for inserting new roll-in tee nuts (or taking them out) without having to dismount the extrusion.

### 2021-12-28

- Fairly significant number of changes today.
- Added a number of missing brackets in the model. I *believe* they are all present now, but will check WBIO (when back in office).
- Fixed a few naming issues in the part codes list. Working on consistency and logical grouping. Re-numbering will come WBIO.
- Iterating through the models and making sure all fasteners are present.
- Added a TPU vibration damper between the AB stepper mounts and the frame. I will test TPU washers WBIO.
- Fixed minor issues with tensioner assembly/disassembly.
- Inset M3s on the tensioner top and added chamfers for screw head insertion/removal.
- Removed #97 after integrating wire guide into the right top `XY Joint` piece (#8).
- Entire XY axis assembly has fasteners but the hotend and X gantry.
- Z axis now has all fasteners; fixed Z2 stepper mislocation.
- Deleted #95 `Wire Guide` part ID entry, as the anchors are doing just fine.
- Trying to modify the side panels for the new crossbars but running into Fusion issues.

### 2021-12-27

- Finished rear exhaust and tagging pieces with IDs for the skirt.
- Publishing 104-111 and reserving 112 and 113 for the display (to be done when back in office).
- Fixed up the electronics undercarriage file with parts already designed.
- Added PSU to the model and desgined a power supply mount, as well.

### 2021-12-26

- Significant work done on skirts:
- Designed frame and section system. Front panels are modular and replaceable but fit together with screws.
- Finished 92mm fan intake, right switch panel, two identical center grille pieces.
- Work for screen and front communications ports can be done once back in office.
- Rear panel has two grilles and two fan cutouts, plus an IEC panel mount spot.
- Not entirely satisfied with fan cutouts, will work on them in the morning and push everything tomorrow.
- Added #s 100-103, the caps to cover the exterior frame edges at the base and top.

### 2021-12-23

- I needed to bring a buck converter with me, so added #85 for a 5A DROK mount.

### 2021-12-22

- Preparing for vacation, so slowing activity.
- Significantly cleaned up wiring in undercarriage area.
- Added Marlin firmware modifications to source tree. Eventually switching to Klipper, but this is functional.
- Slight modification to the SKR2 board mount to improve clearance beneath.
- Created a Raspberry Pi board mount.

### 2021-12-21

**IT PRINTS.**

- Working on firmware for lighting. May need to open an issue with Marlin or push a fix to get two light strips synced with different controllers. First controller (BTT 12864 display) follows the lighting pattern, the second is static.
- Testing a patch to `printer_event_leds.h` and `printer_event_leds.cpp`. It requires adding another preprocessor flag, but it seems to work.
- Printing at 120mm/s and 0.16mm layers okay. Blower needs a higher minimum cutoff.
- Reintroduced Y axis frame bracing to reduce frame vibration during Y axis moves.
- Modified light channel to have deeper siding.

### 2021-12-20

- Finished all crimps but ABL.
- Started mapping headers and began Wiki with corresponding article.
- Tested limit switches, fans, thermistors, bed heat, and finally first hotend heat and filament extrusion.
- Designed mount for programmable LEDs. Design is parametric based on spacing, PCB width, and LED count. Includes a zip tie anchor.
- LED tests. SP901E is finicky with WS2815, leaving it out for now.
- Nearly all connectors are now labeled.
- Resolved display issue.
- Added a modification of an old PTFE tubing coupler design. This part should go away in later revisions.
- First print should be tomorrow.

### 2021-12-19

- Recrimped (properly) all but three of the JST SM connections. Generic crimper for the XH and PH connectors arrived, so went ahead and finished the connectors for all three harnesses above the electrical undercarriage.
- Created an 80mm fan mount for cooling the steppers. Will upload after verifying the second print fits.
- Mounted the Octopus.
- Started work on skirt layout, including IEC (power in) and power switch location.
- Crimped even more wires.

### 2021-12-18

- Fixed emboss on right patch panel
- Revision 2 of XY Joint wire guide. Dealing with some elephant's foot.
- Added a file for extending spare T slot underneath for mounting equipment. The file is parametric for the end-user's modification.
- Designed clamps for board mounting
- Added screw holes to board tray to secure it in place.
- Modified blank tray template and exported STEP file to `/CAD` folder.
- Rebuilt Octopus tray from template file.
- Threw out the last four entries about clamps and boards and went with a simpler design with fewer parts and easier mounting.
- Boards mount at an angle for easier access from the front.
- Made parts for both Octopus and SKR 2 (1.4 if you can find it anymore)
- Started plotting out Octopus fan header usage (cleaner and simpler for now than using SKR 2 + bucks)

### 2021-12-17
- Fixed issue with patch panels.
- Terminated wires, probably terribly, but at least have the lengths and wrap done. Will re-crimp properly later (before using the wires).
- Finished up the `T Slot Wire Anchor` design.
- Tested panel mount--will need to be moved backwards.
- Added a wire guide for the right `XY Joint` to keep the harness elevated.
- Redesigned wire panel mounts to sit further back, leaving more room for exiting wire.
- Added a folder for test GCODE and a basic movement test file, though it needs...testing.
- Modified Z limit switches to lower them 6mm.
- Discovered issue with BLTouch mount after attaching cable ties. Will probably try and move mount position forward a few mm.

### 2021-12-16

- Finished labeling wiring panels.
- Documented part names for consistency and added info to the Readme.
- All parts with wires now have 2-3 letter codes for commonality of labels on connectors and panels.
- Designed panels for left and right side to connect wiring.
- Created `Electronics Master` file for undercarriage area.
- Working on wire anchors/guide channels
- Will start testing lighting channels at some point soon.
- Crimped way, way more wires today. Probably done crimping until the JST-PH connectors arrive.

### 2021-12-15

- Tested XY motion
- Designed and tested replacement for Z bottom bracket that includes rail alignment.
- Tested all endstops
- Added build plate
- Sketched up panel mounts for JST-SM connectors for 2-6 pins and fit-tested
- Began setting up wiring for JST-SM
- Added STL Filename column to `Part Codes`
- Crimped a lot of wires.
- Created file for tracking wire codes and terminal names

### 2021-12-14
- Fixed some issues with the left pulley component.
- Fixed an incorrect peg hole depth on right mid `XY Joint`.
- Added 5mm to the AB stepper mounts.
- Pushed Y limit switch out ~20mm to allow clearance for the X limit switch. This is hacky, but will work and keep the bed area available.
- Adjusted screw holes on right pulley component to account for the new limit switch mount.
- Designed Bowden mount for BMG.
- Designed `Gantry Lock` for servicing hotend and belts.
- Raised the Y limit switch a bit to give clearance for heated inserts in the mount.

### 2021-12-13
- Fixed up some Tony Table issues
- Created a Y rail alignment guide for in front of the tensioners
- Right `XY Joint` now has attachment points for zip ties and a guide for wiring.
- Right `XY Joint` now has additional room (1mm) for cut tolerance on the X axis extrusions/linear rail and heat growth for both the same.
- Adjusted height of XY pulley components to allow for 0.2mm difference in height of the milled Y rail.
- Fixed some issues with the Left `XY Joint`'s bottom piece.
- All `XY Joint` belt guides are now at roofed at 35 degree angles instead of the prior 45 degrees. This shouldn't be an issue with print difficulty and will give additional belt clearance.
- Ditto `Stepper Pulleys`.
- Added `Y Axis Rail Guide` parts for both sides on the `Stepper Pulleys` components. *The Y limit switch mounts on this guide*.
- Spent part of the day learning to crimp JST-SM pins and replacing Blender's heater cartridge (terminated in JST-SM, but also what Clock 3 uses)
- Added `X Limit Switch Mount`
- Published to a public repository.
- Dropped the fan duct about a millimeter to get it to blow under the nozzle (hopefully).

### 2021-12-12

- FPD and second iteration for part cooling duct. The front half is from the EVA project, modified for heated inserts.
- Redid all gantry core fastener locations to make room for other parts.
- Working belt clamp design.
- Created a Tony Table with part codes.

### 2021-12-11
- Assembled second X gantry print--much better clearances around the hotend and fit is good.
- PTFE collar issue resolved with a brace on the mounting bracket
- Added fourth screw hole to extruder mount and relocated to ensure flat connection.
- Added zip tie anchors on front mount plate for wiring.
- Started work on belt tie-offs.
- Updated part color-coding and ran into some Fusion bugs.

### 2021-12-10
- Installed bed frame of correct length. Bed is now a complete unit and finished.
- Installed new lead screws (500mm).
- X axis extrusion and Z crossbar should both arrive today for proper kinematics testing.
- Still having 12864 display issues.
- Modified the hotend mounting bracket to have an install point for ABL.
- Created a BLTouch bracket (what I have on hand).
- There is now a working mount for the BMG + stepper of arbitrary depth. Included cutouts for mounting with wires sideways.
- *Frame is now current to spec*.

### 2021-12-09
- Testing bed height adjustment screw with a locking thumbscrew, similar to the Ender 5's Z endstop trigger.
- Working in earnest on hotend mount and cooling. 
- FPD for V6/BMG mount.
- Testing `PTFE Collar` to allow PTFE tube from extruder to be removable and reattachable easily.
- Started work on paneling.
- Added a few missing joints.
- Added clearance to edges of X axis by rounding the `XY Joint` fronts.

### 2021-12-08
- Tested new limit switch arrangement to raise bed.
- Adjusted limit switch design.
- Reassembled `XY Joint`.
- Some adjustments to `Z Gantry` and `Lead Screw Plates`.
- More limit switch design tweaks to maximize volume.
- Finished bed wire support design.
- Added linear rail stop to raise maximum bed height with identical build volume.
- Working towards shortening filament path for hotend when the `X Gantry` comes together.
- Need to stiffen up new limit switch, but that can wait.
- Pursuing modular panel cutouts for flooring to simplify design and add flexibility for later.
- Modeled full exterior frame and brackets
- Combined frame and internal parts into `Master` file
- Lots of additions to `Parameters` file and fixes

### 2021-12-07
- Organized files, now tracking STLs with a naming scheme in a spreadsheet
- Fixed misnumbered and nonsequential parts
- Lots of work to fix endstop issue and raise Z bed max
- Several iterations to fix small issues with the XY Joint (no longer XY Interface)
- Actively working towards a hotend arrangement design
- Switched to button head screws for most printed parts on the test rig
- Designed cable support piece for the bed wires

### 2021-12-06
- Worked around X axis linear rail
- Adjusted XY interface for linear rail on bottom
- Modeled X gantry and hotend
- Tested cooler ideas, explored EVA as a COTS option (belts incompatible)

### 2021-12-05
- Worked on Z axis all day
- Z limit switch designed, printed, and tested
- Fixed issues with Z steppers after too much troubleshooting
- Added several files for components
- Making switch to button head screws to avoid recesses to socket head.
- Tested bed auto align
- First time with working Z kinematics!

### 2021-12-04
- Finished printing FPD Z axis parts
- Spit and polish to Z stepper mount designs
- Assembled Z axis minus limit switches

### 2021-12-03
- Lots of Z axis fixes and tweaks
- FPD of bed frame bracket
- FPD of printed Z gantry
- Finished `Z Master` file containing full Z motion
- Created XYZ master integrating XY and Z master files, will add frame

### 2021-12-02
- FPD for stepper mounts and bearing holder (prototyped in PETG to get more printers involved)
- First test of heated inserts on tensioner piece with press--went well
- Adjusted all parts to ensure press inserts holes are included where needed
- Added Z frame to `Parameters` file
- Created `Z Frame` file to assemble Z components with
- Folder cleanups, moved old stuff, reorganized `Assemblies` folders
- Finished heat pressing all tensioner parts
- Mounted first AB stepper and bearing holder, printed second
- First XY kinematics test (manually moving tensioned belts)

### 2021-12-01
- Renaming Clock 3 to Snow Angel to avoid confusion with Voron Clockwork extruder. Sigh.
- Completed FPD of right side for XY interface, refined left.
- Calculated first two frame cuts, started labeling frame for machining
- Stole X linear rail for Z axis. Will order a higher quality one for the X.
- Adapted Clock 2 limit switch plate for Y axis and made a template for the other axes.
- Ordered Clock 2 -> Snow Angel frame pieces
- FPD for tensioner (they mirror, so only one design)
- Added belt guide channel for right y gantry
- Continued to refine tensioner
- Added rail stops to X axis, built into the XY interface top pieces.
- Prelimary Z work
- Most of the design done for AB stepper mounts and internal bearing to help align the drive rods.

### 2021-11-30
- Cleaned up stepper pulley plates after assembly
- XY Interface design started
- Completed first printable design (FPD) for left side of XY interface (where X extrusion mates with the Y linear rail carriage)

### 2021-11-29
- Created XY Master file
- Swapped in braces with center threads
- Fit tested stepper pulley plates

### 2021-11-28
- Lots of work on the rear idlers and stepper pulleys
- Disassembled most of test printer
- Pieces will now be numbered and have a L or R designation where applicable.

### 2021-11-27

- Created a `clock-3` branch and started organizing files
- Expanded layout file
- Finished full belt path in layout file and added offset planes for frame and belts
- Still determining exact belt Z offset, as much of the design depends on that

### 2021-11-26

- Created a layout file for inserting derived parametrics and sketches
- Started breaking out parameters
- Sketched 3-point Z layout
- Did a quick pass at designing the stepper pulley bodies to look for issues in the layout file
- Created a hole diameter test block and brass insert practice block, inaugurating the `Tools` folder.

### ~2021-11-25

- Picked it back up again. Time for a redesign.
- Planning 3 point Z, smaller, tighter enclosure
- Switched to F695 idlers from F688 to save ~1/4" of width and depth.
- Working on a switch to brass inserts now that I have a press for them.

### Break

Life got involved.

## Q3 2021

### 2021-08-19

- Back to printing Linear Bearing Mounts.
- Planning to install wiring harness in center-rear.
- Fit tested new limit switches (Ender 3-style).

### 2021-08-15

- Printed and assembled simple PETG hotend mounting plate. The entire gantry cart for the hotend is now in finished PETG except the backside belt attachment component.
- Proceeding with Mini Fit Jr connectors for (nearly) everything.
- Installed heatsinks on alpha and beta steppers

### 2021-08-12 - 2021-08-14

- Resolved print issues
- Currently one Linear Bearing Mount printed, waiting on filament.
- Printed second Z endstop and updated firmware configuration.

### 2021-08-11

- Reprint of two Linear Bearing Mounts
- Test print for a corner bracket cover
- Reworked hotend carriage's belt fastening a bit. Added guide channels around the backside for working blind to center the belt.

### 2021-08-10

- Installed insulating washers.
- Installed finished feet.
- Installed new 204020 extrusion for above door.
- The hole for the linear bearing has too little clearance with my current print settings. Doing tests to find a balance.

### 2021-08-09

- Worked on aligning Z axis components
- Continued printing PETG bed parts
- Printed TPU feet
- Designed insulating washer for between the underside of the bed and the hex nuts

### 2021-08-08

- Started assembling and mounting print bed & frame
- Glued heatsinks on to alpha and beta steppers
- Attached PETG endstops
- Testing PETG Z limit switch mount
- More minor PETG parts
- Designed bracket cover

### 2021-08-07

- First Tr8 nut mount print
- Designed Linear Bearing Assembly
- Designed Bed Mount Alignment Spacer to properly center and align bed.
- Added limit switch bumper to nut mount
- Added Z limit switch mount
- New Alignment Spacers for Z Axis assembly.
- Minor appearance fixes.
- Continued refining bed components.

### 2021-08-06

- Restarted Z axis work
- Got Tr8 nut mount nearly designed
- Fixed up component tree, added Internal Assembly
- Assembled bed & swapped in more threaded brackets

### 2021-08-05

- Got to a good place on the hotend/belt mount components
- Designed the X Axis Limit Switch Bumper and Endstop (I need a shorter name for this)
- Attached the hotends on a simple mount. There's no way to raise or lower them (nor a print bed yet) but it gives me a moving test object.
- Working on hotend wire management and clamping belts.

### 2021-08-04

- Continued redesinging hotend/belt mount
- Integrated hotend to X gantry
- Replaced X rail stops with Y axis rail stops, need to redesign x limit switch bumper.
- Reorganized a lot of files.
- TPU printed files are now color coded a teal color.
- Started an Internal Assembly file integrating frame and components.

### 2021-08-03

- Printed final tensioners
- Fought with Fusion
- Redesigned hotend mount
- Redid Frame model from scratch.
- Modeled off-brand BCZAMD version of Bondtech's BMG ALU mount.

### 2021-08-02

- Finished reassembling both Y gantry carts and got the X gantry extrusion on.
- Iterated on tensioner design
- Printed stepper caps

### 2021-08-01

- Assembling X gantry at new height
- Designed new tensioners through several iterations. The new design is much narrower and sleeker. Also uses a shorter screw.
- Stepper alignment caps need redesign
- Inserted super thick brackets to the frame. Minor fixes.

### 2021-07-31

- Reassembling piece by piece to check for issues and square frame.
- Need to reassemble again to inset more spring-loaded t nuts and to record for instructions.
- Alignment shims now slide in to the extrusion or some other guide to prevent slippage.
- Moved X axis extrusion up 4mm to simplify logistics for screws and raise the nozzle.
- Redid floor of Y gantry carts for PETG printing

### 2021-07-30

- Finished frame brackets and fasteners, needs review
- Started printing parts in PETG.
- 80mm alignment spacer for base alignment added
- Added more pre-assembled fasteners with screws and tee nuts
- Disassembled test frame for reassembly to new specs

### 2021-07-29

- Designed Y endstop switch mount
- Lots of small polishing
- Added alignment piece for the stepper mounts
- Preformatted brackets added
- Alignment spacer for the Y axis crossbars added
- Completed frame, working on inserting all brackets and fasteners

### 2021-07-28

- Endstop switch work

### 2021-07-27

- Second pass at back piece, adjusted hole sizes for standoffs
- Initial X endstop design. Wrong way; flipped to home to the right.
- Mounted hotend gantry test.

### 2021-07-26

- Fusion is crashing again/still.
- Started hotend gantry design
- Assembles in three main pieces, finished the MGN12H carriage section in the middle.
- First pass at back piece for belt mounting.

### 2021-07-25

- Finished up V1 of the bed, still needs polish
- Now have a mount for leadscrews.
- Redesigning the jigs for the Z axis to be slightly narrower.

### 2021-07-24

- Started designing bed
- Got initial size in place, 510mm x 260mm for frame, re-using Z axis struts that are going to be widened.

### 2021-07-23

- Z Axis needs to be setup *first* or it's going to be difficult.
- Strugged with Z axis all day.

### 2021-07-22

- Fusion crapped itself. Again.
- Looking in to endstop positioning. 
- Will home to the front-right, so considering that aspect.
- Designed jig for Z axis
- Steppers will all have 2mm or 3mm thick covers on the their mounting plates to hold the 35 metal spacers in place and add additional spacing for the 45mm screws.
- 35mm spacer + 3mm plate + 3mm printed spacer = 41mm, leaving 4mm to screw in to the stepperi

### 2021-07-21

- Printed and finished linear rail stops
- Adjusted height of tensioners (off by 5mm)
- Tested XY kinematics
- Started design of Z axis 

### 2021-07-20

- Assembled full belt system
- Designed gantry lock for servicing belts and hotend
- Designed end stops for X and Y axis linear rails

### 2021-07-19

- Worked on belt system
- Printed various tensioner iterations
- Assembled working right tensioner and installed one belt.
- Adjusted wall thicknesses & offsets for tensioner. Fixed a few issues and tested a lot of bad ideas.
- Tensioner now acts as endstop for Y axis linear rails on the front side.

### 2021-07-18

- Moved out extrusions in the X axis. Ideally will resolve spacing and alignment with shorter X axis rail or 60mm wide front extrusions connecting the interior and exterior frames.
- Tweaked and assembled right Y gantry.
- Moved Y axis rails backwards to add more room for hotend.

### 2021-07-17

- Finished stepper pulley/rear idlers component.
- Assembled stepper pulley/idler blocks.
- Continued work on Y gantry.
- Finished printing Mk2 of the Y gantry. No major snags.
- Mk1 belt tensioner designed
- Began tensioner printing

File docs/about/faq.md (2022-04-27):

---
title: Frequently Asked Questions
summary: Answers to common questions.
authors: Jon Harper
date: 2022-04-09
---

*This document is actively being refined and edited for mistaeks.*

## General Questions

### Why another 3D printer?

!!! note
    TODO This is a longer story that I'd like to get right.

### Can I get a kit from somewhere?

That would be super cool, but not at the moment.

### Can you build one for me?

No, but a Bill of Materials is in the final stages of verification and formatting. In addition, documentation on the assembly and configuration process is ongoing.

### Will you come work for my company?

Hey, that's a cool idea. [Here's my LinkedIn](https://www.linkedin.com/in/jonspaceharper/). Reach out and we'll find out.

## Conceptual

### Why so many lock washers?

A bag of 500 lock washers costs not much more than 100. A builder will need more than 100 lock washers no matter what I do, so I standardized on M5 screw + lock washer + tee nut where it is reasonable to do so.

Also, Loctite eats ABS if it's not completely dry, and there's a lot of it in this printer.

### Why a V6 hotend instead of [x]?

Several reasons:

- V6 clones are readily available and generally only differ in length with respect to compatibility
- the mount interface can be reused for other hotends that are "groove mount" style, like the newer Dragon hotends.

### Why does the Z axis not have a third driver?

That's on the todo list for the future. Given time and cost constraints, two steppers has to do for now. With silicone columns and a BLTouch for assisted leveling, it's less a problem than a "nice to have".

I have studied the RatRig design and find their three-point leveling design exceptional. Future iterations of this project may adapt a similar bearing-style magnetic mount.

### Why not a larger build volume?

I strongly considered this, but settled on the Creality CR-10 form factor. Going larger starts becoming quite troublesome:

- Overall increase in cost beyond 310x310mm
- Power usage scales nonlinearly, as bed volume scales quadratically and chamber volume cubically.
- CR-10 build plates are cheap and readily available. 350mm build plates (and larger) are harder to come by.
- A 300mm^2 build plate can still reasonably be heated with a built-in DC heater. Larger areas require AC pads, which means adding a relay, a cutoff, more wiring...and more risk if mis-installed.
- The Z volume is limited somewhat by the stepper being placed outside of the chamber. This necessarily sacrifices about 150mm of thread, and a 500mm lead screw is already hard enough to get aligned.

*However*, MIC-6 aluminum build plates are plentiful enough now that a future revision of this project will likely switch over to using one.

### Why don't you use M4 screws?

To keep the number and type of screws down. This project is made entirely of M3 and M5 screws with the exception of the bed and PSU, which both require M4 fasteners for mounting.

## Materials and Sourcing

### Do I have to use the same brands for materials (e.g. Misumi)?

Most of the printer is substitutable with OEM materials. Although initial support is only provided for the BIGTREETECH Octopus MCU, a FYSETC S6 or Spider would theoretically work just as well. The only part that can't be substituted without major work is the Raspberry Pi.

### There is a really good supplier that sells custom [x]. Why don't you use their product?

I'm avoiding single-source parts (Raspberry Pi and MISUMI door frame notwithstanding). Ideally this will keep costs down as well as prevent supply and sourcing issues.

### Can I use Neopixels (WS2812B, 5V) instead of WS2815 (12V)?

Yes. You can even use a different driver, like APA102, as long as it uses no more than 4 wires (VCC, GND, and one or two data). The SP901E is a data repeater and compatible across a range of voltages. That said, you may see a small difference in lighting quality with a 5V LED string like the Neopixel due to voltage drop across 2 meters of wire.

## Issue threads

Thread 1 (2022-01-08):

(Part 104) Ethernet port panel mount profile is incorrect

jon-harper, 2022-01-08:
Current profile is off and required cutting with an x-acto knife to fit. Panel cutout is approximately 1-2mm high, but need to determine if this is related to the part I purchased.

Closed 2022-02-13.

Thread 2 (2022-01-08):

Tensioner design could be improved

jon-harper, 2022-01-08:
The current invertible tensioner design is both bland and a little confusing: the screw is above on one side and below on the other. This is okay, but because it's hard to see, it's not intuitive. Consider redesigning.

jon-harper, 2022-02-18:
I fixed the issue. It's not directly related to a redesign, so this remains open.

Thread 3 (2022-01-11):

XY Joint: wire anchor is weak

jon-harper, 2022-01-11:
#8, right top XY Joint needs a different, sturdier attachment to the base.

Maybe wrap the raised lip around the hemisphere for the wires and extend the center lip to front of the anchor?

jon-harper, 2022-01-17:
Resolved with the 1/14 redesign. Forgot to close this.

Closed 2022-01-17.

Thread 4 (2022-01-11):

Make insert holes cone shaped

jon-harper, 2022-01-11:
Insert holes are currently set in the `Parameters` file as 4.1mm. Set to a larger diameter at an angle TBD.

jon-harper, 2022-01-18:
I've added a Heated Insert Testing Block

After testing, 4.5mm with a -4 degree taper is a good default when printed on the XY planes **and** YZ/XZ planes. I still need to update the parametrics, so I'll leave the capability to change the values in place. Once I use up this roll of filament, I'll rerun the tests with an ABS+ to see if they differ at all.

jon-harper, 2022-01-18:
Okay, resolved. All STLs are updated to reflect the new default and the taper angle is now parametric in the model.

Closed 2022-01-18.

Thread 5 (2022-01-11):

Reorder ID tags

jon-harper, 2022-01-11:
Currently the part IDs are slightly scattered and a bit mismatched. They also do not allow for alternates, like a version of a panel with and without a cutout.

Plan to renumber parts with either sequential part numbers for versions or some other method (e.g. appending 'a', 'b', etc.)

jon-harper, 2022-02-09:
ID Sequences:

- 000-500 Printed parts
- 500-599 Screws and Fasteners
- 600-699 Transmission (Bearings, Pulleys, Lead Screws, Rods and Rails)
- 700-799 Extrusions and Brackets
- 800-899 Electronics
- 900-999 Misc
- 1000+   Hotend Components

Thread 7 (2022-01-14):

23/24: Z Stepper Mounts need redesign

jon-harper, 2022-01-14:
Goals:

- Quicker print
- Added wire anchor spots
- Designed around thrust bearing

jon-harper, 2022-01-22:
Thrust bearings have arrived. Using F8-16M bearings (8x16x5mm).

jon-harper, 2022-01-22:
This is still important, but I've removed the priority label because it's not critical to moving ahead.

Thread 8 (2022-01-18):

Panels need sketches for fabrication

jon-harper, 2022-01-18:
Panels are not yet finished.

*Edit:* Due to plastic costs, particularly with the styrene shortage, I'm proceeding with 0.2"-0.25" (~5-8mm) **wood** panels.

Need:

- ~~To determine thicknesses (sides, floors, top, and inner panels)~~
- Method of attaching inner and outer panels to PIR foam and one another
- Determine color

jon-harper, 2022-02-18:
As of 2/18, side and rear panels are done.

jon-harper, 2022-02-21:
Enough work is done on the panels that I'm going to close this.

Closed 2022-02-21.

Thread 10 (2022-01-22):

Bill of Materials needed

jon-harper, 2022-01-22:
Bill of Materials is not available yet.

This is dependent upon completion of the filtration system and paneling design in the model.

jon-harper, 2022-02-09:
This is partly related to #5 but not dependent upon its resolution.

I've created a part system that can be auto-extracted from the Fusion model to create a BOM, either whole or component by component. This may need finessing for top-level items that would be excluded from a component-by-component approach, e.g. individual fasteners for the panels are in the top level model and nowhere else.

jon-harper, 2022-02-09:
Requires resolution of #20 (all parts need a number).

jon-harper, 2022-02-12:
Remaining pending portions of the BOM are

- an appendix set of entries for odds and ends
- filtration system entries
- verification of part counts and IDs

jon-harper, 2022-02-13:
Filtration system is finalized and generating a good BOM.

jon-harper, 2022-02-16:
I'm going ahead and closing this as I've generated several BOM already. There's polish to be done in pulling in extra information, customization, and presentation, but it's good enough for now.

Closed 2022-02-16.

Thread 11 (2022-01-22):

Air Filtration prototype incomplete

jon-harper, 2022-01-22:
Pending:

- ~~Completion of vertical prototype~~
- ~~1" ID hose for 75mm fan exhaust~~
- ~~Chamber testing~~

jon-harper, 2022-02-05:
The actual hose diameter was 20mm. As inconsistent hose sizes *will* be an issue, the CAD files should include a parametric intake.

A parametric exhaust is also likely when we get some paneling done (see #14).

Closed 2022-02-05.

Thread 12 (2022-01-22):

Prototype needs reassembly and documentation

jon-harper, 2022-01-22:
Pending resolution of the following issues:

- #10, Bill of Materials
- #8, panel assembly/testing
- #11, Working filtration prototype.
- #13, Gantry Lock Bar
- #18, Door Assembly and Testing
- #27, BOM Appendix

jon-harper, 2022-03-03:
Currently verifying an initial BOM against the model to correct inconsistencies. This should close soon.

jon-harper, 2022-03-09:
Soon is a relative term.

Closed 2022-03-19.

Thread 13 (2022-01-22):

Gantry Lock Bar needs redesign

jon-harper, 2022-01-22:
We'll need gantry lock bars for proper dis- and re-assembly.

Closed 2022-02-06.

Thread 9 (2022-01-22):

Air filtration system needs either its own repository or better organization

jon-harper, 2022-01-22:
Currently the air filtration components do not rely on the ID system, nor is the filter dependent upon Clock 3 itself. Since the air filtration components can be re-used for other projects, consider another repository.

jon-harper, 2022-02-13:
Now tagging with part numbers to include in initial BOM. Will fork into another repo later.

In summary:

- Parts are now tagged with PN part IDs
- Next push will include renamed printed parts, with irrelevant parts removed.

Closed 2022-02-13.

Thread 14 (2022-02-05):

Add parametric tool files to /CAD folder

jon-harper, 2022-02-05:
- ~~Exhaust hose~~
- Electrical T-slot mount (to use short off-cut 2020 sizes for the undercarriage)
- ~~LED guide~~

Other items may be added to this list.

jon-harper, 2022-02-12:
Added heat set insert tools to CAD folder, even though they’re not in the list.

Closed 2022-02-17.

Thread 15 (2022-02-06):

Raspberry Pi should be horizontally mounted

jon-harper, 2022-02-06:
The current orientation requires the board be mounted backwards for the connector extensions to reach the front panel mounts. This blocks any airflow.

jon-harper, 2022-02-17:
Fixed with last commit--forgot to tag issue #.

Closed 2022-02-17.

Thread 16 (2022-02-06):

Skirt panels: 92mm fans are oversized; reduce to 80mm

jon-harper, 2022-02-06:
The 92mm fans are definitely too much (a habit from my early 2000's computer case cooling interest). Reducing to 80mm will both save on cost and sound a lot better.

Consider optional TPU fan gaskets.

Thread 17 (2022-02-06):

Door gaskets

jon-harper, 2022-02-06:
The front door will need TPU gaskets around the edges. There is a ~2mm lip around the entire edge, so about 3-4mm of TPU should do it and provide ample excess. Can also be cut to size with periodic screw holes.

jon-harper, 2022-02-24:
After #18 , found door gap varies from 4.5-5mm when fully level and 4-6mm when allowed some slack.

jon-harper, 2022-03-28:
With 3mm acrylic panels, now have a 3mm gap. Cannot work on this until panel fabrication is completed.

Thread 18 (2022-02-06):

Door Assembly and Testing

jon-harper, 2022-02-06:
- ~~Need to order door panels from MISUMI~~
- ~~Assemble and measure~~
- Measure for issue #17 to get TPU thickness correct

jon-harper, 2022-02-09:
All units mm

Door Frame: 620x700
Outer: 614x696
Inner Panel: 577x659
Extrusion Length 1: 564
Extrusion Length 2: 646

jon-harper, 2022-02-24:
Door gap varies from 4mm to 6mm, 4.5-5 when fully level.

Closed 2022-02-24.

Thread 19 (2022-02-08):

Eliminate M5 x 10mm screws from the bed

jon-harper, 2022-02-08:
The bed has 3mm thick metal plates. Add in a lock washer and that's initially 11mm, reducing to 10mm available when tightened (6mm of travel in the 2020, 3mm plate, 1-2mm for washer). An 8mm screw won't be able to reach to engage the nut threads, but adding a washer or two will allow us to use M5 x 12mm screws instead.

jon-harper, 2022-02-10:
Switched to M5x12 with an added washer.

Closed 2022-02-10.

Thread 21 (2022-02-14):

SP901E is not modeled

jon-harper, 2022-02-14:
I've created a placeholder with a part number and fasteners to keep going with the BOM.

jon-harper, 2022-02-16:
Added on hold tag. The SP901E may or may not work, so it doesn't make sense to take time modeling it until I know it is needed. Additionally, it's in the auto-generated BOM, so I've achieved what I need to so far.

Closed 2022-02-16.

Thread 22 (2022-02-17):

Improve BOM scripts

jon-harper, 2022-02-17:
## Overview

Certain items, particularly pertaining to wiring, are difficult to model or are measured in by distance instead of instances. They should be added to the BOM separately.

The short term solution is to add a fixed set of line items to the BOM, but this prohibits customization. A more elegant solution would be to either prompt during BOM generation to customize the output *or* to iterate the model and adjust based on which parts are visible/flagged as enabled in some way.

I'm comfortable with writing Python against an API, but scripting this all would decouple the data for each part--where known/associated--and place it in the build script. I'd rather store the data in the model itself and extract it.

Perhaps have a dialog that prompts for customization, then enabled or disables certain components or adjust parametric values before walking the component tree? Or, decouple customization, and have a button to customize the *model*, then generate a BOM based on that?

## Steps

1. Open Master file
2. Run `customize.py`
3. Customization script modified default values, makes invisible or otherwise removes any unnecessary components
4. Run `stl_export.py`
5. STL export script then exports any parametric STLs (e.g. LED guides)
6. Run `bom_export.py`
7. BOM script iterates over the model and extracts needed values.
8. Any extra, unmodeled parts can either be added as properties of the components they are related to or stored in the script itself.

## `customize.py`

This part requires some more acquaintance with Autodesk's Fusion API, but it's based on Qt's architecture. I've seen nothing surprising in the documentation thus far. Fusion's API is much simpler for creating GUIs than Qt's, so creating a customization dialog should be simple.

It will take more effort to determine 1) how much to customize and 2) how to internally deploy those changes in the model. The simplest starting point is a skeleton dialog that switches between direct drive and Bowden by changing object visibility. This will get *really* complicated with the connector panel, however. It may be best to widen the panels to maximum possible width (e.g. leave room for 5 wire connectors, even when 3 wires are used).

## `stl_export.py`

I'm not going to look into this as the moment, but it's definitely an idea for the future. Auto-exporting either a few parametric files or even whole shebang would be great...but not right now.

## `bom_export.py`

The kernel of this already exists as `ExtractBOM_PN.py`. It needs modification to export as a .csv or similar and to check the model for whatever day `customize.py` leaves it about parts that are not modeled.

## Summary

Regardless of the level of scripting, it seems best to store as much data as possible directly in the model. Perhaps even add a "wire_count" and "wire_gauge" parameter to components that need them. If component C is enabled and C contains `wire_count` and `wire_gauge` properties, add distance D multiplied by `C.wire_count` of wiring gauge `C.wire_gauge` to the bill of materials. This *may* get harder for counting connectors and types.

jon-harper, 2022-03-28:
This is resolved with the creation of the [Clock3Scripts repo](https://github.com/jon-harper/Clock3Scripts).

Closed 2022-03-28.

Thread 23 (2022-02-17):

Redesign hotend wiring harness

jon-harper, 2022-02-17:
The hotend is currently entirely removable by disconnecting all of the wires. Adding a removable panel mount that screws in place would greatly simplify the wiring situation. This would require revering the male/female connector direction, as the panel mounts should come from the harness, not the removable components.

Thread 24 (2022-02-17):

Z Gantry needs work

jon-harper, 2022-02-17:
Currently the Z Gantry plates (PN022 and PN023) have four screws fastening them to the bed, but the Lead Screw Plates (PN027 and PN028) only have two. They're also connected by two M3 screws. This can be coordinated with fixing #7.

jon-harper, 2022-02-26:
I have fixed the 4/2 M5 fastener issue, but other issues that should be addressed:

- The two halves should be more securely fastened than they are.
- The lead screw piece is too weak.
- The limit switch sensor should trigger by the lead screw (in front) to aid access to the thumbscrew.
- The linear rail can be moved up 25mm to bring the carriage closer to the lead screw nut and bed, lowering the center of gravity. This means moving up the carriage mounting points.

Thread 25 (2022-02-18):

PTFE tubes and exhaust hose need panel cutouts

jon-harper, 2022-02-18:
The panels now have cutouts for filament on the right and the exhaust hose on the left. They need printed parts that in those gaps.

jon-harper, 2022-02-25:
Forgot to tag this in today's commit--PN120 and PN121

Closed 2022-02-25.

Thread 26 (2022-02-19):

Board mounts are not thick enough

jon-harper, 2022-02-19:
The board mount for the Raspberry Pi is 6mm thick, which leaves just one layer beneath the insert (the hole is 5.8mm deep). This probably affects the other board mounts.

Closed 2022-02-21.

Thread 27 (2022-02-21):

Complete BOM appendix

jon-harper, 2022-02-21:
Things like Superlube, IPA, and squaring tools need to be on the BOM as a "you should have this on hand" section. Other items that are measured in distance and area need to be included, as well.

jon-harper, 2022-03-06:
Nothing surprising turned up during the disassembly process. Likely will continue to keep things like lubricants and zip ties in the appendix list. Heat shrink tubing is probably overkill to count.

Closed 2022-03-06.

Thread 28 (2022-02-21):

Measure length and area items in BOM

jon-harper, 2022-02-21:
Length:

- Wiring (almost 100m!)
- Wire looms
- PTFE tube: 1.7m
- Polyurethane Foam Weatherseal: 1.2m
- Silicone Tubing: 1m
- Belts: 4m

Area:

- Insulation (1x 4'x8' sheet if uncut, 2 if sheets had to be cut for travel)
- Paneling (2x 4'x5' sheets of 12mm plywood, 1x 4'x5' sheet of 5mm acrylic, and about 24"x6" of 6mm plywood)

jon-harper, 2022-03-20:
- All wire runs will now have an ID to aid tracking and assembly.
- Wire IDs are based on component IDs
- IDs not involving the PSU are tailed with a letter code indicating distance from MCU, e.g. HE-A is MCU->chamber panel mount, HE-B is from the right chamber panel to the tooldhead panel.
- There are a few third level connectors with a -C. The modified BLTouch wire is ABL-C and connects to ABL-B. Likewise, I included a -C for LED strips. Even though they are soldered on, they still have to be made by the builder.

Closed 2022-03-20.

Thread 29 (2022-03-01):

Questions for fabrication

jon-harper, 2022-03-01:
- ~~Confirm piano hinge dimensions~~
- Polyiso foam fasteneing method
- Paint or other seal heat tolerance
- ~~Inner panel costs~~ Skipping for now
- Wood preferences
- ~~Wood thickness~~

jon-harper, 2022-03-20:
Got all of my questions answered.

Closed 2022-03-20.

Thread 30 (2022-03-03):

Undercarriage panel mount need rework

jon-harper, 2022-03-03:
~~To facilitate removing the wiring panel mount, there should be cutouts in the bottom of the panel for the wires to slip out. Consider reinforcing the bottom in other ways, This also corresponds with shifting from M3x12mm screws that are too long to M3x8mm screws and removing the front frame.~~

Given issues in the source file, it's going to be easier to start from scratch with the same basic outline. M3x8 screws will be fine with a 4mm thick panel, no frame as a spacer.

Closed 2022-03-21.

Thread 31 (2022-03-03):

Undercarriage fasteners need correction

jon-harper, 2022-03-03:
- PSU uses 4x M4 x 8mm screws, not M3.
- Lock washers can probably be eliminated from the MCU mount.
- Panel mounts are M3x12mm, which is too long. See #30

Closed 2022-03-21.

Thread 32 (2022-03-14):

BOM Script should pull in data and append counts

jon-harper, 2022-03-14:
The Bill of Materials generation script is pretty rough.

1. The script should draw from a source tab-delimited file, then
2. Generate a list of parts and counts, and
3. Export that list with the additional data associated in the source file.

jon-harper, 2022-03-19:
#22 is related to this. The current script *does* as specified, but doesn't have a working UI yet. I'll push the updated script this weekend and get this closed.

jon-harper, 2022-03-20:
Fixed with last commit. Forgot to tag.

Closed 2022-03-20.

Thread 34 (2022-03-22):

STLs are not exported in print layout

jon-harper, 2022-03-22:
This should take a moderate amount of work.

- Create a layout folder in Fusion
- Insert derived components
- Arrange
- Export only from those files
- Organize by component?

jon-harper, 2022-04-03:
Update: nearly all printed parts are in layout documents. At some point in the coming weeks, I will re-export all and close this.

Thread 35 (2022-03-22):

Printed Z Bracket is too short

jon-harper, 2022-03-22:
Floor panels are now 12mm, making the Z bracket (PN019) far too short. 13mm tall will allow M5x20mm and will look nice.

This issue should be coordinated with #7 and #24, as it will change the height of the linear rail.

Closed 2022-03-23.

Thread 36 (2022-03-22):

BOM Export tool does not have a UI

jon-harper, 2022-03-22:
This is pretty critical to an initial release, although the utility is functional now.

jon-harper, 2022-03-28:
This is resolved with the creation of the [Clock3Scripts repo](https://github.com/jon-harper/Clock3Scripts).

Closed 2022-03-28.

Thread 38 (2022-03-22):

Stepper Pulleys are missing two screws on top.

jon-harper, 2022-03-22:
Stepper pulleys need an additional:

- 2x M5 x 12mm
- 2x M5 lock washer
- 2x M5 roll in tee nut

jon-harper, 2022-03-23:
Fixed.

Closed 2022-03-23.

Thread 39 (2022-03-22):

LED guides should use drop-in tee nuts instead of roll in.

jon-harper, 2022-03-22:

jon-harper, 2022-03-23:
Fixed. Forgot to tag in commit.

Closed 2022-03-23.

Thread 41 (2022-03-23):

USB C buck converter is not modeled

jon-harper, 2022-03-23:
A STEP file would be great. I'll model it if I can't find one shortly.

jon-harper, 2022-03-23:
And now it is.

Closed 2022-03-23.

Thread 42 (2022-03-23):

A/B steppers should be tailed with JST-SM

jon-harper, 2022-03-23:
Right now the A/B steppers have ~1.2ish meter long wires. They should be tailed properly with JST SM and have a detachable cable.

Closed 2022-03-26.

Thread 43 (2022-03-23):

Fusion 360 script to visualize t-nuts is needed

jon-harper, 2022-03-23:
It would be extraordinarily helpful to be able to isolate *just* the t-nuts and frame to assist counting and identifying location

jon-harper, 2022-03-24:
This is being developed into a Fusion 360 add-in. In the coming days I will probably create a mini-repo for it.

jon-harper, 2022-03-28:
This is resolved with the addition of the [Clock3Scripts repository](https://github.com/jon-harper/Clock3Scripts)

Closed 2022-03-28.

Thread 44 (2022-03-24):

Documentation needs centralization

jon-harper, 2022-03-24:
- What work is done so far on documentation planning needs to be centralized for tracking, particularly with respect to media and loose notes that can get lost.
- Fusion exports .avi files for assembly videos--need a web-suitable converter to for assembly instructions
- Wiki template?
- Use the wiki or GitHub Pages?

jon-harper, 2022-04-01:
Created a separate git repo to hold docs. Can then use gh-pages branch to display compiled markdown or run Jekyll.

Closed 2022-04-01.

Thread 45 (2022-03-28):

Micro Fit 3.0 Panel Mount profile needed

jon-harper, 2022-03-28:
Switching to Micro Fit 3.0 connectors for the hotend means new panel mount profiles are needed.

This affects PN070, the right electrical panel, as well as any redesign of the hotend harness with a panel mount (issue #23 ).

jon-harper, 2022-04-01:
Delayed by mis-delivered package.

jon-harper, 2022-04-08:
Update: profile is in; still needs testing.

Closed 2022-04-11.

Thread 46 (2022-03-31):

BLTouch should use Octopus TFT header

jon-harper, 2022-03-31:
Right now the BLTouch connection uses the built-in Dupont headers. The TFT header right next to it is unused, provides 5V, GND, and two signal pins, which is precisely what we need, but with a JST XH connector.

jon-harper, 2022-05-21:
This may not work properly. Closing.

Closed 2022-05-21.

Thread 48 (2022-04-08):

Split Bill of Materials into Sales and Manufacturing

jon-harper, 2022-04-08:
The BOM needs to be fully disambiguated to a Sales BOM (purchased items, lit. materials) and a Manufacturing BOM (finished parts for assembly).

Notable issues:

- Heat set inserts should be in the materials category
- Cut-to-length parts like PTFE, weatherseal should have a fixed entry in materials and another with length from the parts list.
- Cables should all get part numbers of a new category in the form CN123, as none are modeled and all are default values; some are purchased and others fabricated.

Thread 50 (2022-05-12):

ABL mount point is poorly located

jon-harper, 2022-05-12:
Testing shows the ABL mount should be mounted on the side of the cooling fan intake shroud, rather than on top of the cooling duct. This allows sliding the ABL mount up/down, whereas that's not an option when it sits on top of something.

Closed 2022-05-21.

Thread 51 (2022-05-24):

Model/Prototype Assembly Inconsistencies

jon-harper, 2022-05-24:
Ongoing list of parts to add or remove from the model.

- +2 PN577 for Raspberry Pi
- +6 PN530 for Idler Pulley Plates
- -6 PN578 for Idler Pulley Plates
- -6 PN532 for Idler Pulley Plates

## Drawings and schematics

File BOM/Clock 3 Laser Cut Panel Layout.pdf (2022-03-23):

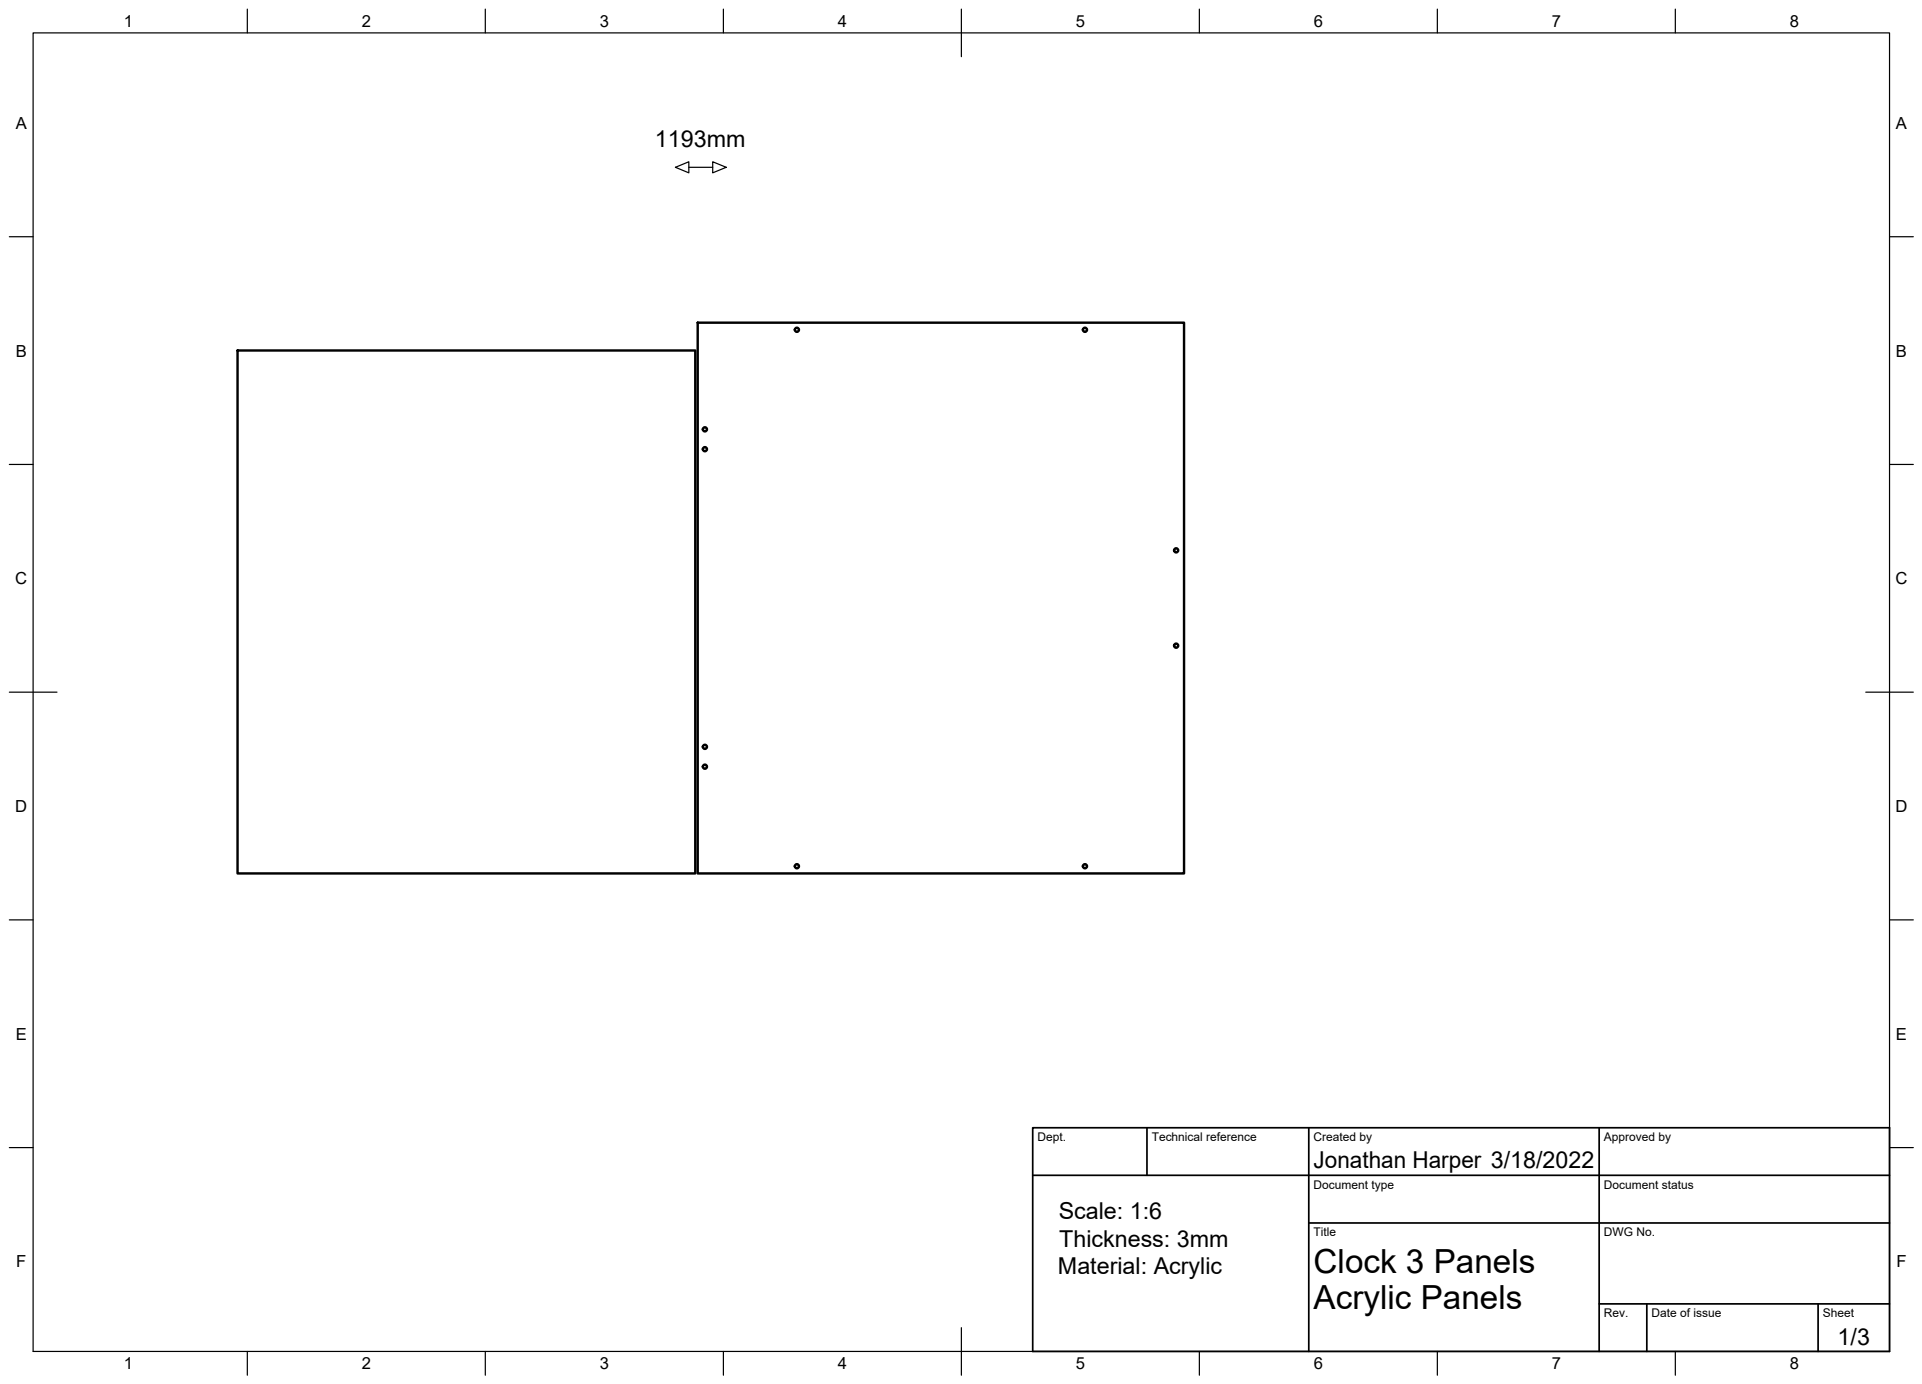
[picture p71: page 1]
Title; DWG No.; Rev.; Date of issue; Sheet; Acrylic Panels; Clock 3 Panels; Scale: 1:6 Thickness: 3mm Material: Acrylic

Dept. | Technical reference | Created by Jonathan Harper 3/18/2022 | Approved by

Document type | Document status

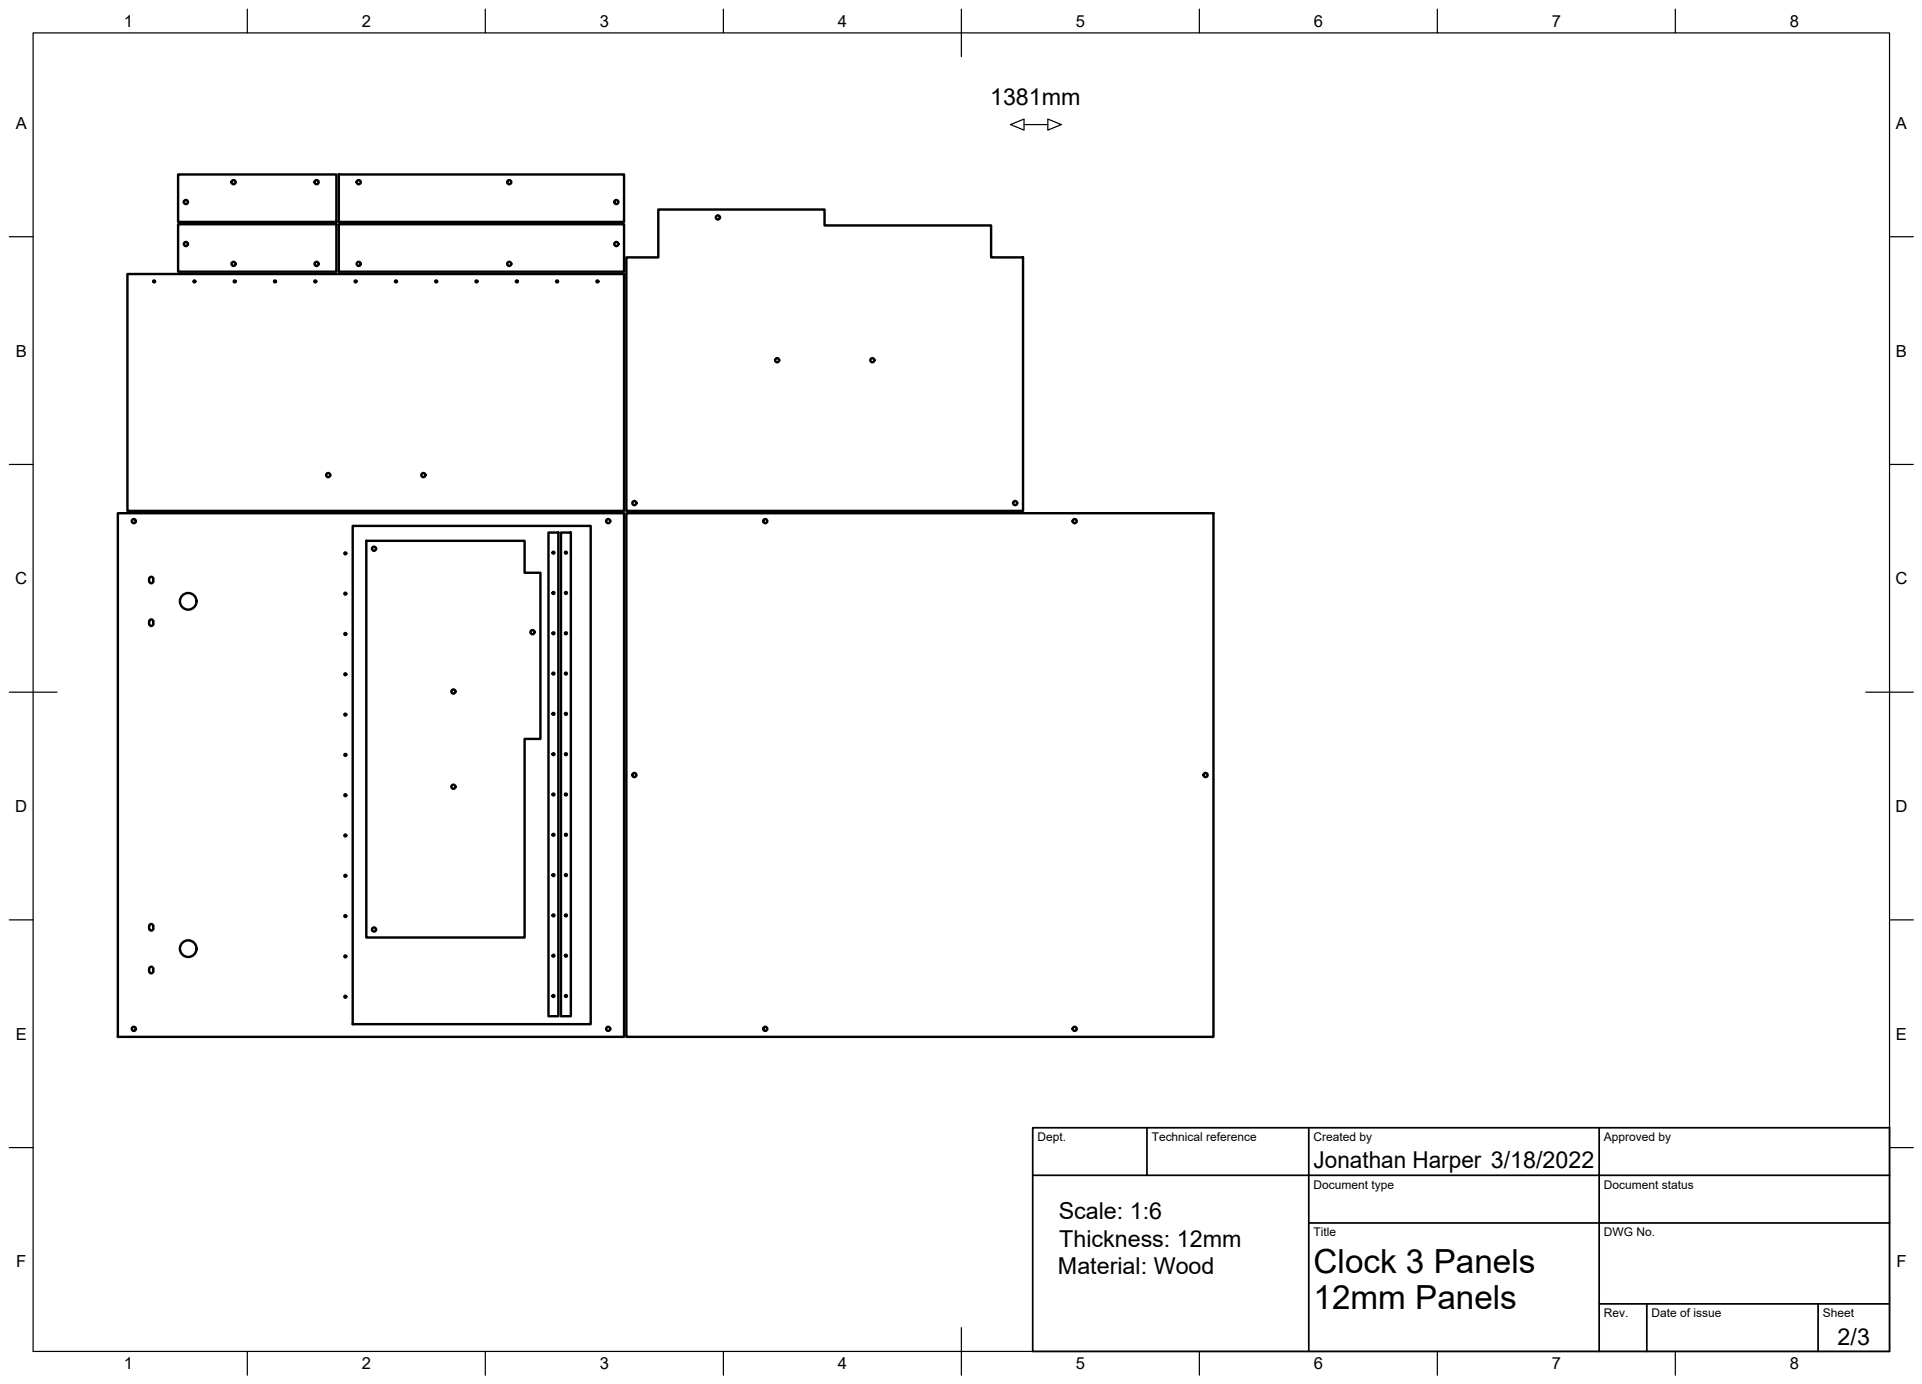
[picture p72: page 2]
Title; DWG No.; 12mm Panels; Clock 3 Panels; Scale: 1:6 Thickness: 12mm Material: Wood

Dept. | Technical reference | Created by Jonathan Harper 3/18/2022 | Approved by

Document type | Document status

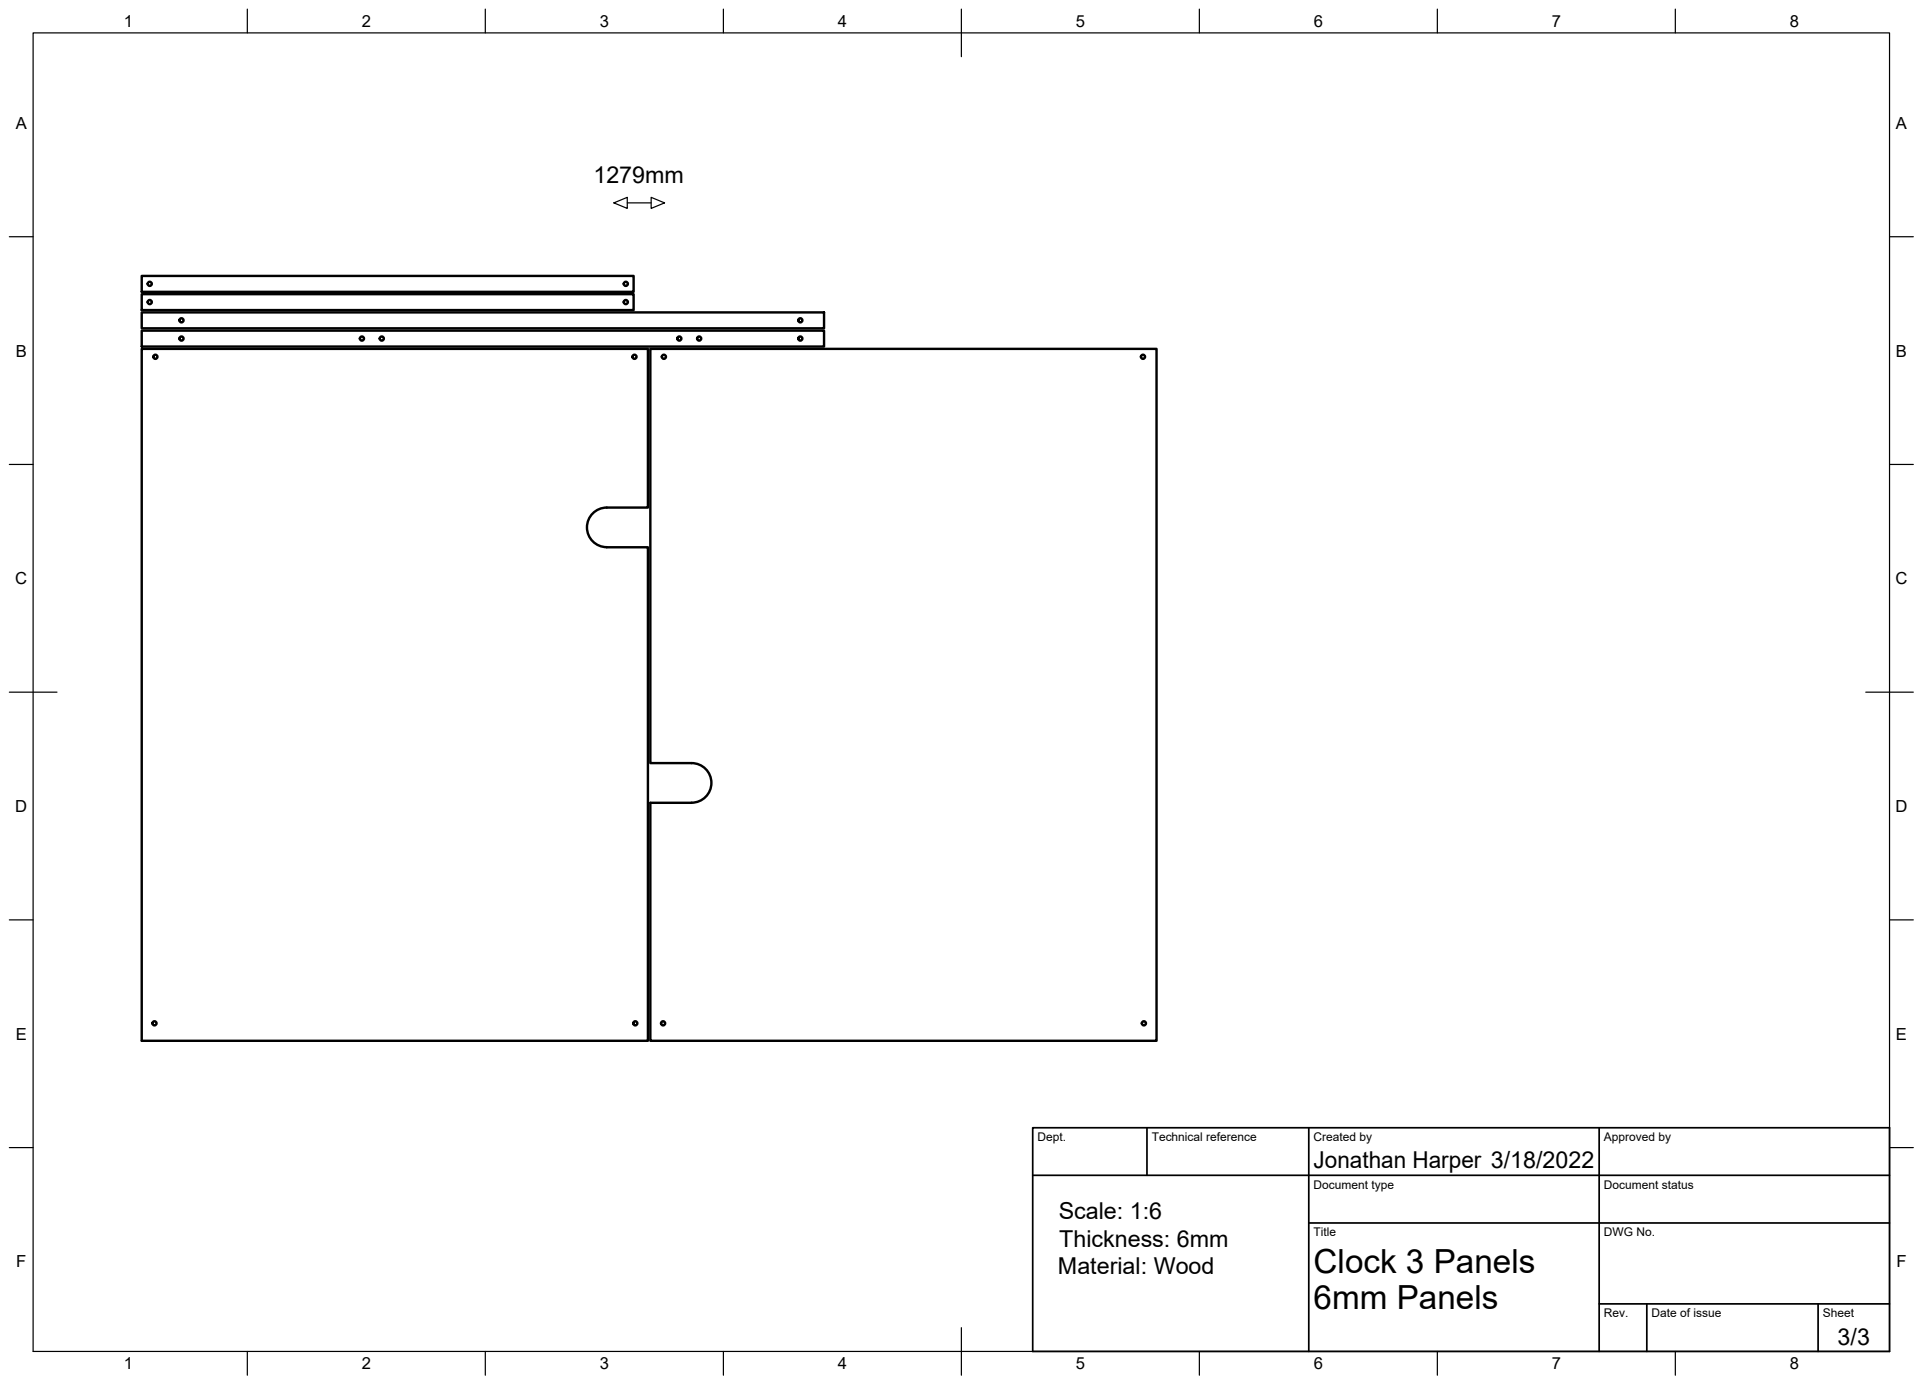
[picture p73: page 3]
Title; DWG No.; 6mm Panels; Clock 3 Panels; Scale: 1:6 Thickness: 6mm Material: Wood

Dept. | Technical reference | Created by Jonathan Harper 3/18/2022 | Approved by

Document type | Document status

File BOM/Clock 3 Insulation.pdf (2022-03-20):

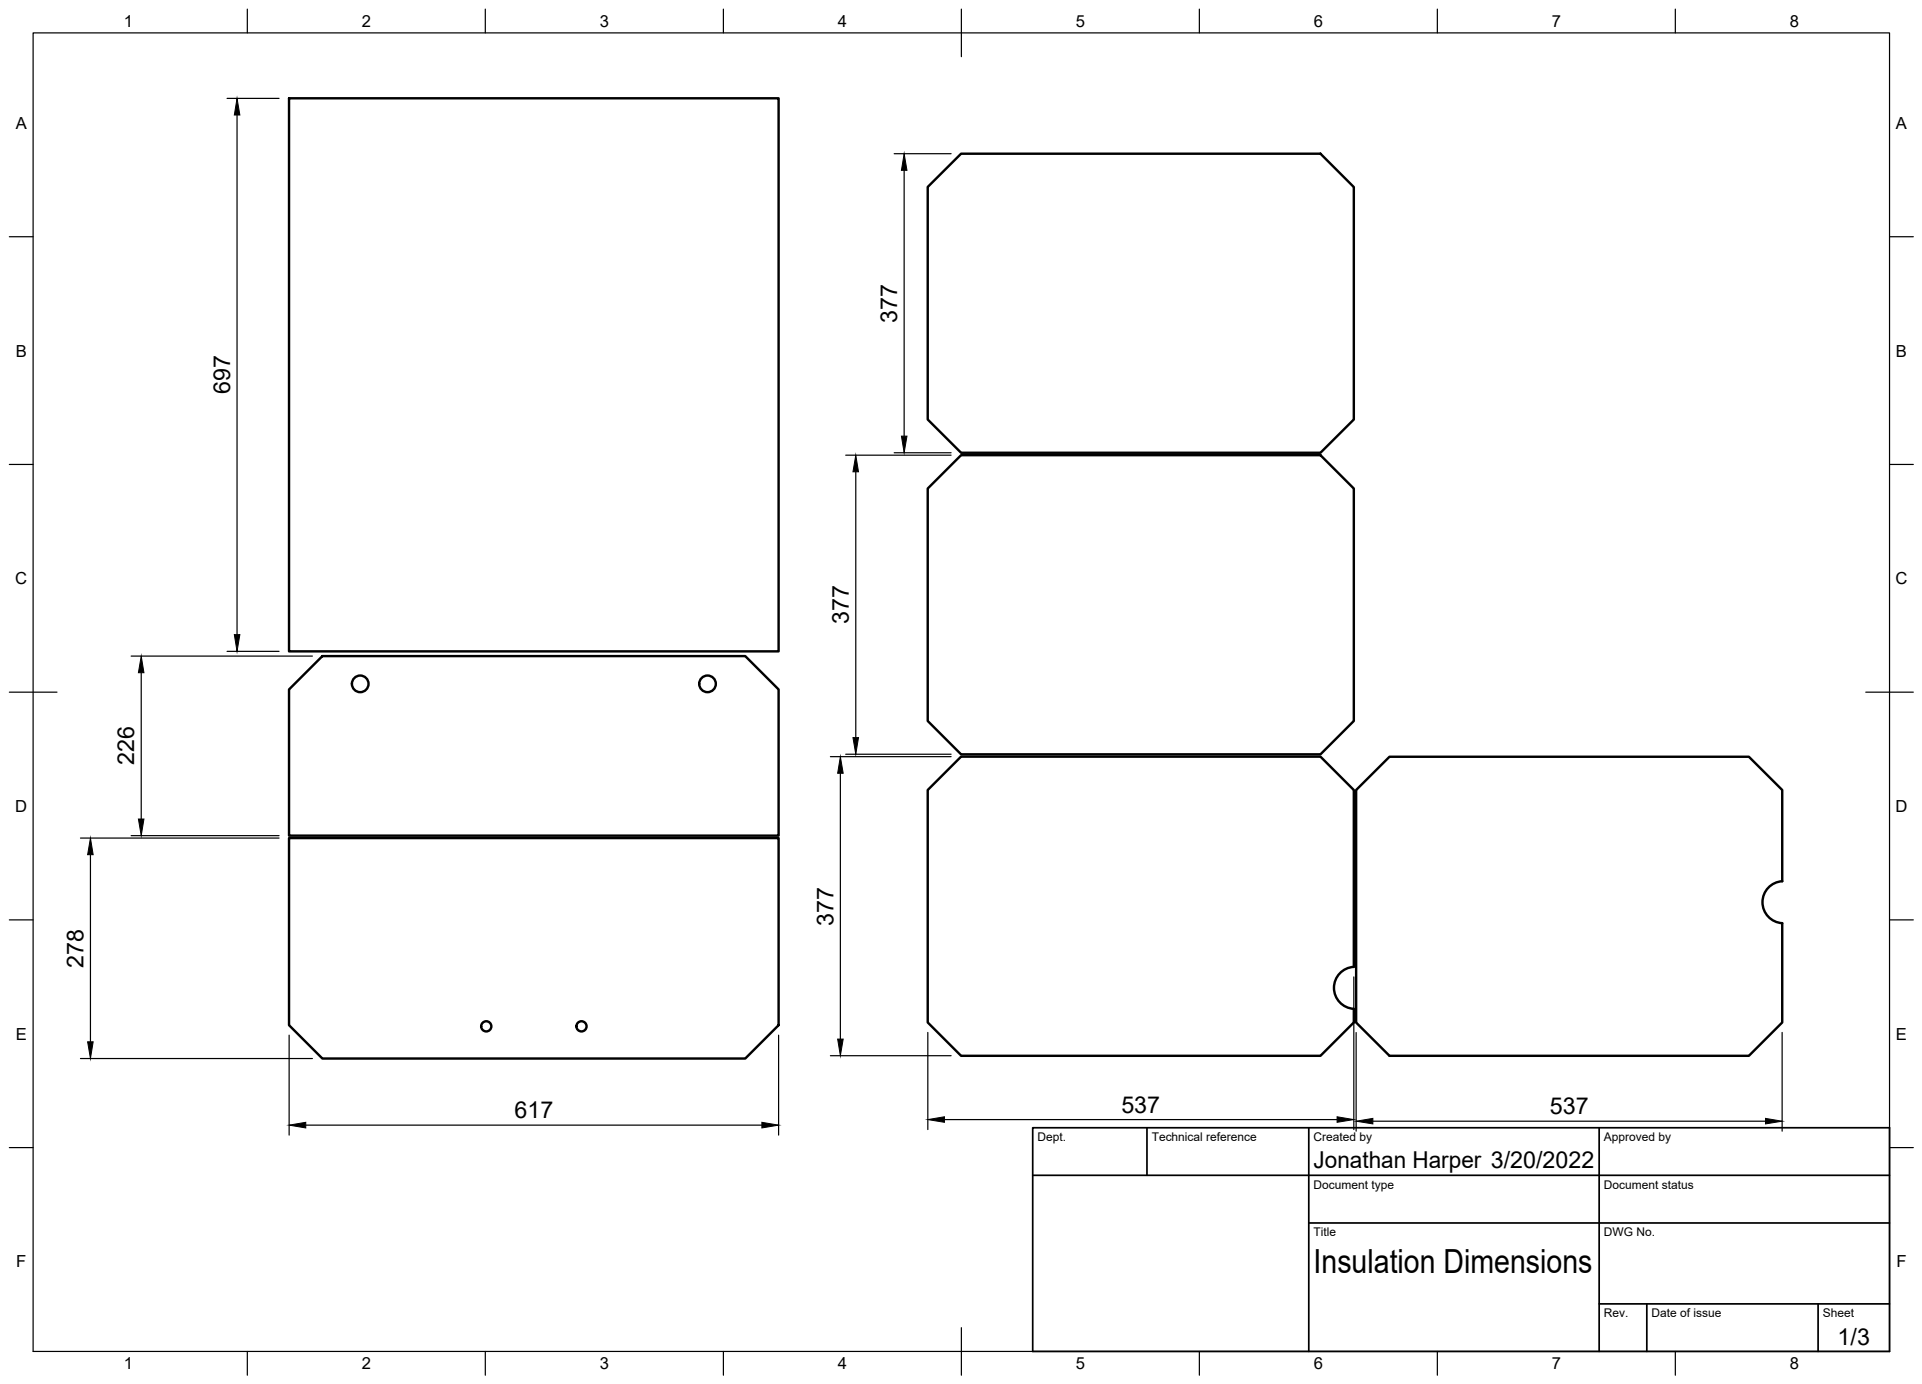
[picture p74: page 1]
Title; DWG No.; Rev.; Date of issue; Sheet; Insulation Dimensions; Jonathan Harper 278

Dept. | Technical reference | Created by 3/20/2022 | Approved by

Document type | Document status

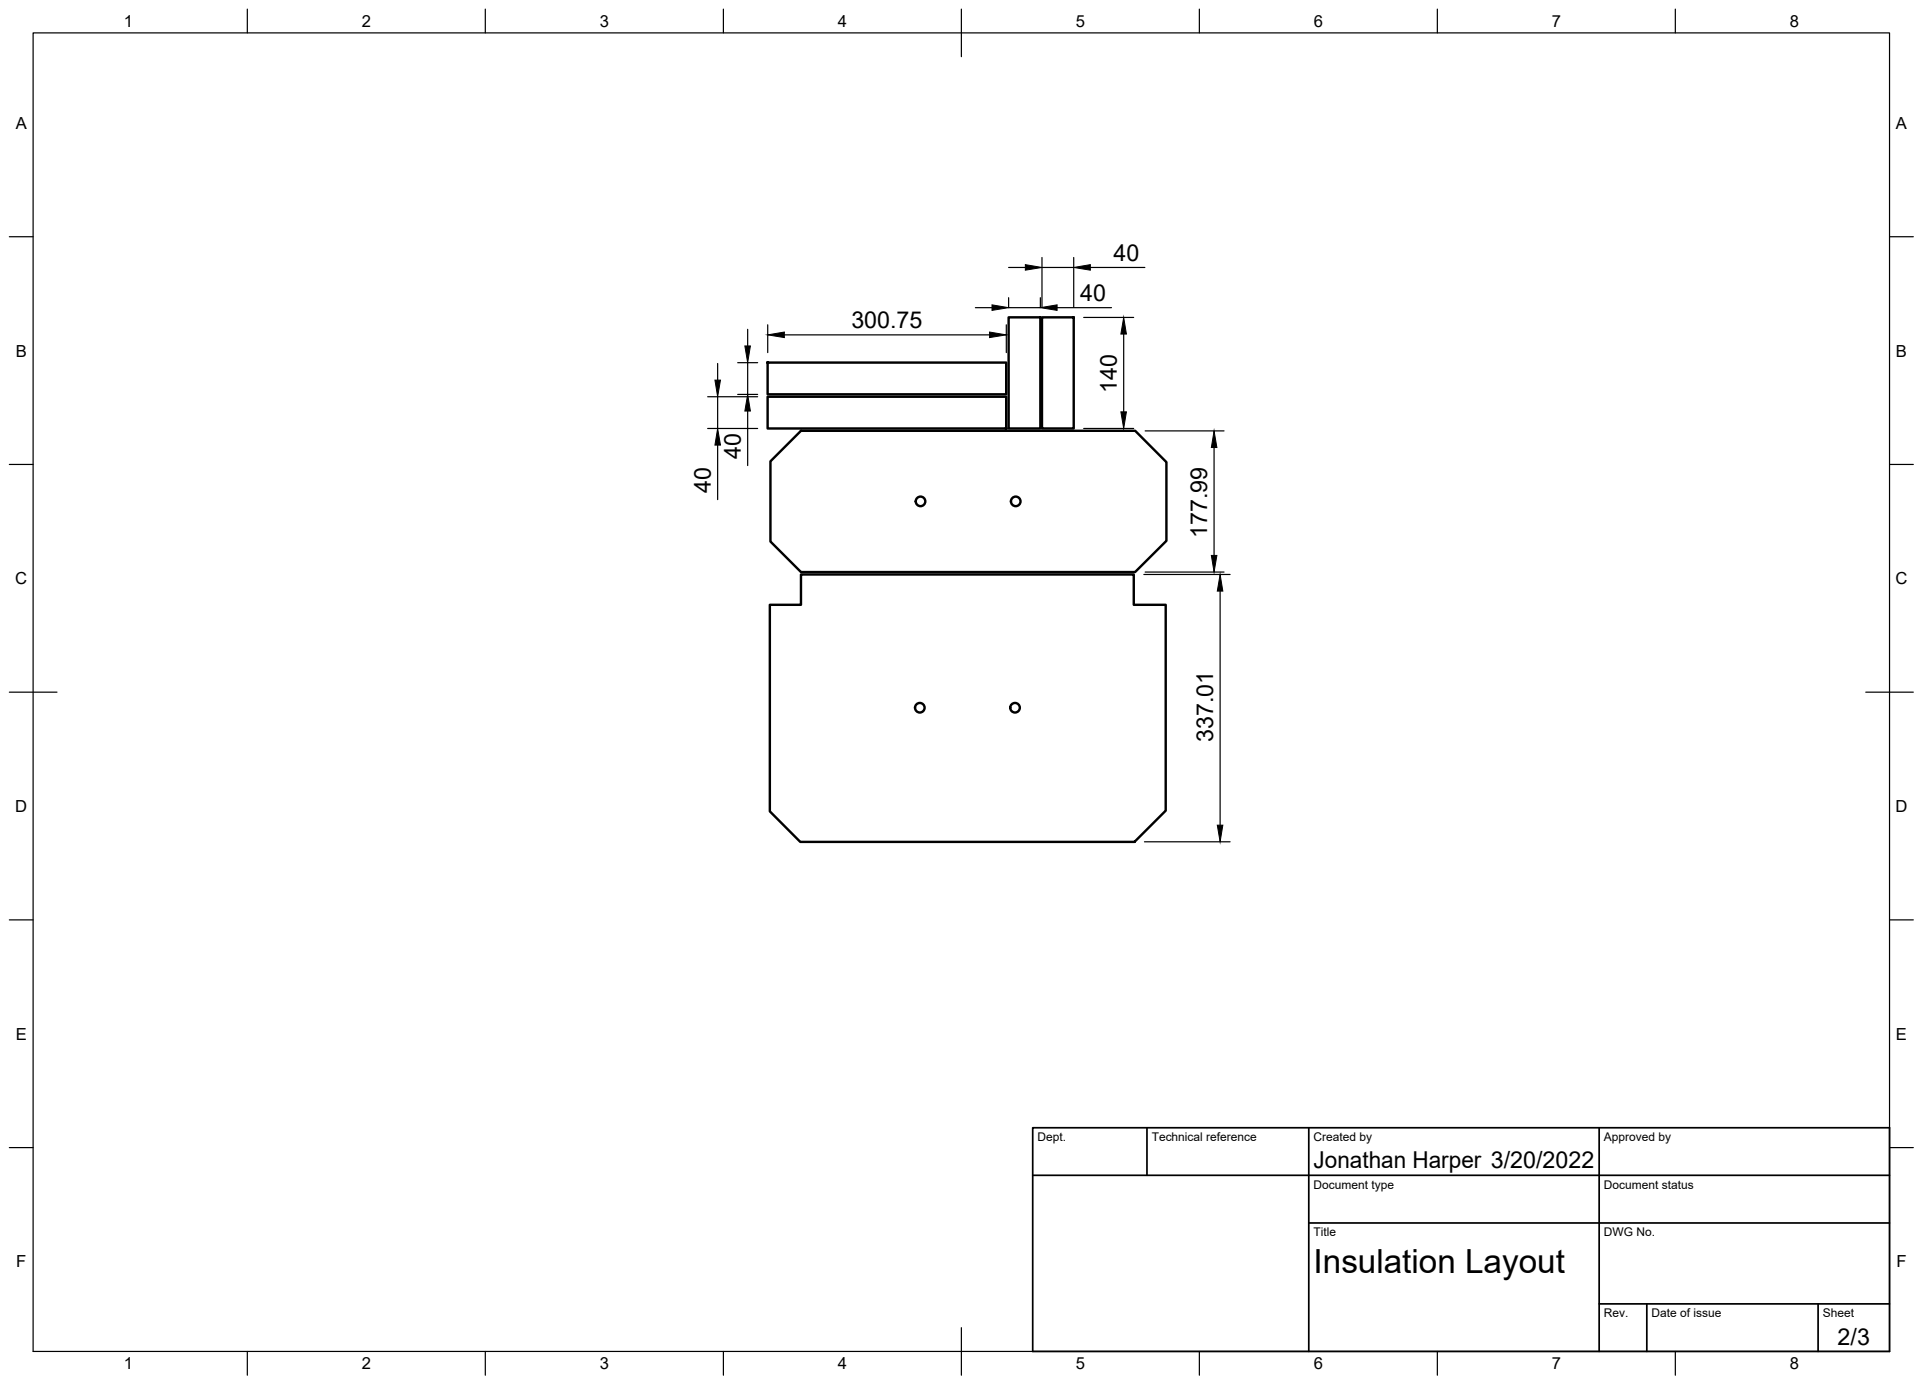
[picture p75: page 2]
Title; DWG No.; Insulation Layout

Dept. | Technical reference | Created by Jonathan Harper 3/20/2022 | Approved by

Document type | Document status

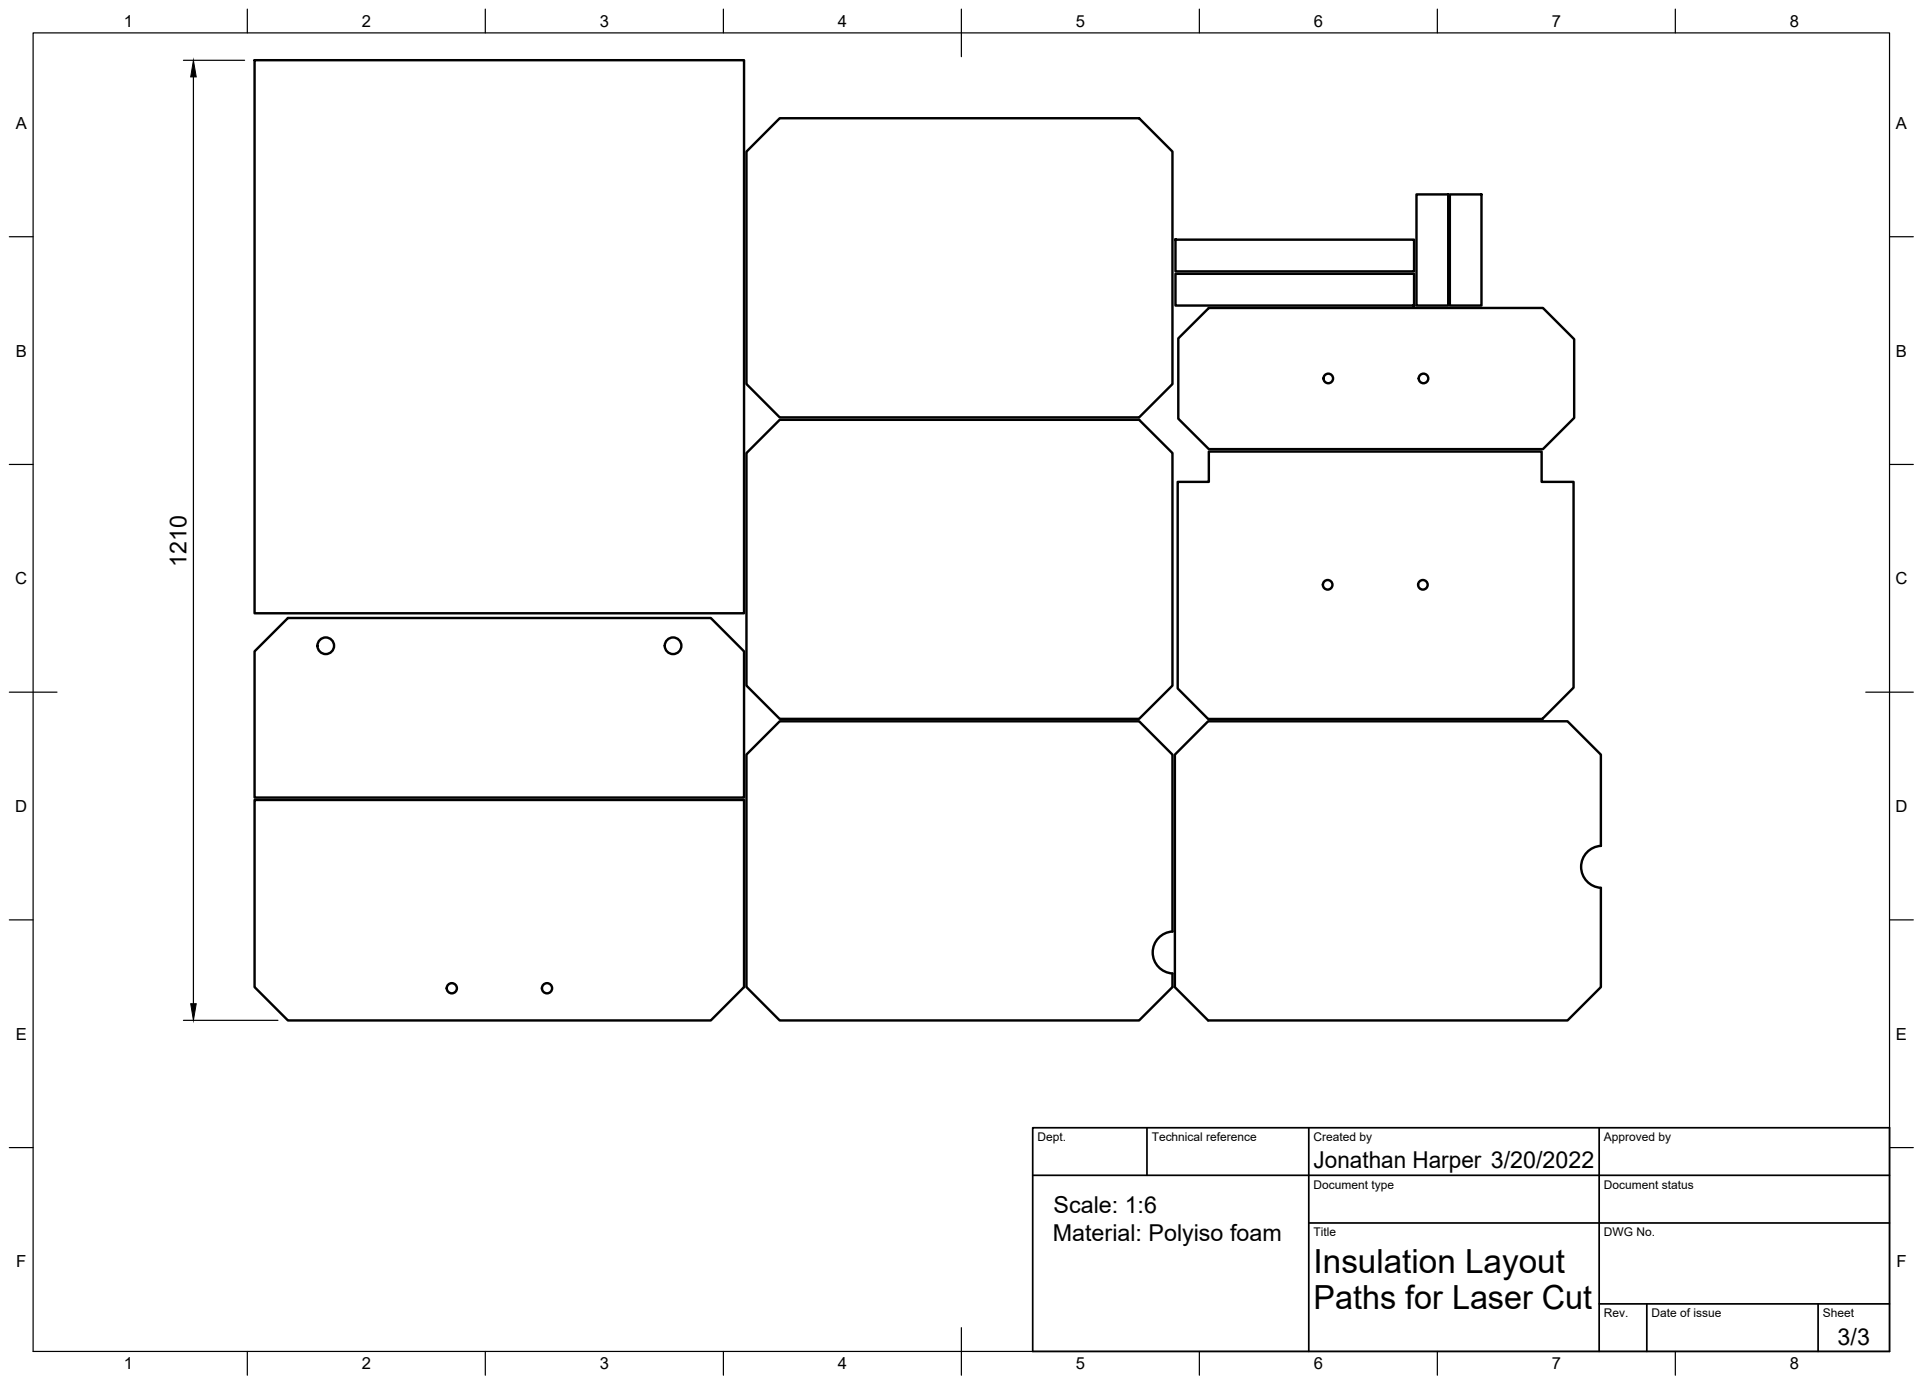
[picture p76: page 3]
Title; DWG No.; Scale: 1:6

Material: Polyiso foam 1210

Dept. | Technical reference | Created by Jonathan Harper 3/20/2022 | Approved by

Document type | Document status

Insulation Layout
Paths for Laser Cut

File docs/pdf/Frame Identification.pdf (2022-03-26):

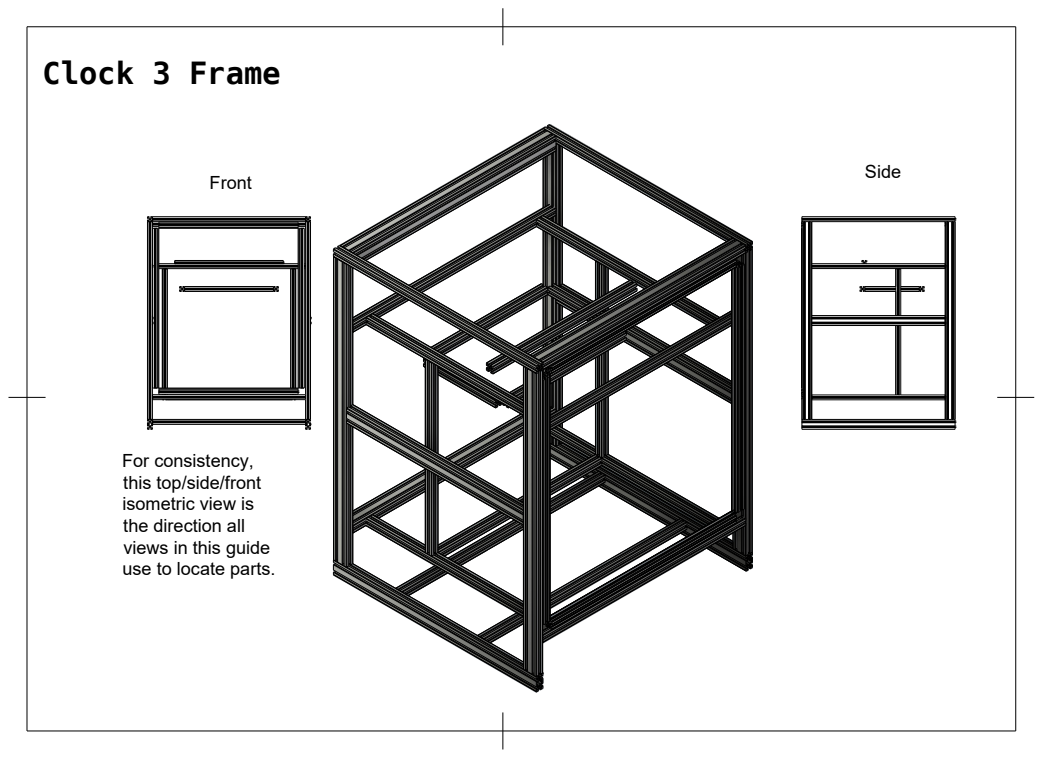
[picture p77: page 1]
Clock 3 Frame

For consistency,
this top/side/front
isometric view is
the direction all
views in this guide
use to locate parts.

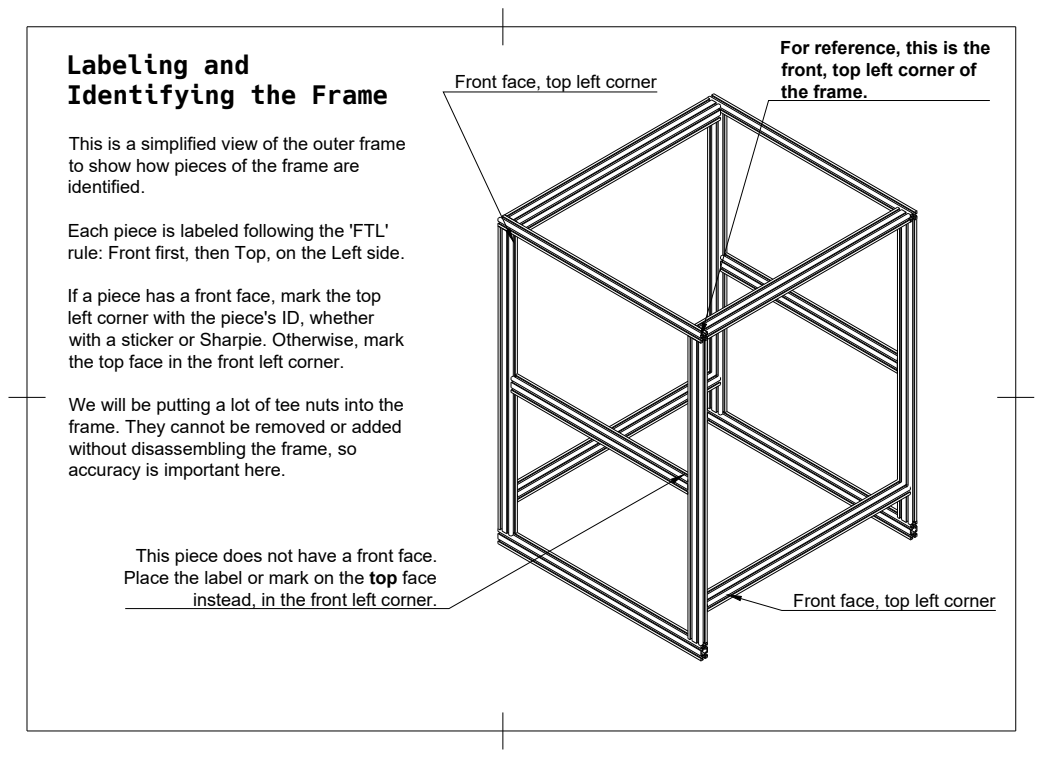
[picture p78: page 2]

For reference, this is the
front, top left corner of
the frame.

Labeling and
Identifying the Frame

Front face, top left corner

This is a simplified view of the outer frame
to show how pieces of the frame are
identified.

Each piece is labeled following the 'FTL'
rule: Front first, then Top, on the Left side.

If a piece has a front face, mark the top
left corner with the piece's ID, whether
with a sticker or Sharpie. Otherwise, mark
the top face in the front left corner.

We will be putting a lot of tee nuts into the
frame. They cannot be removed or added
without disassembling the frame, so
accuracy is important here.

This piece does not have a front face.
Place the label or mark on the top face

instead, in the front left corner.

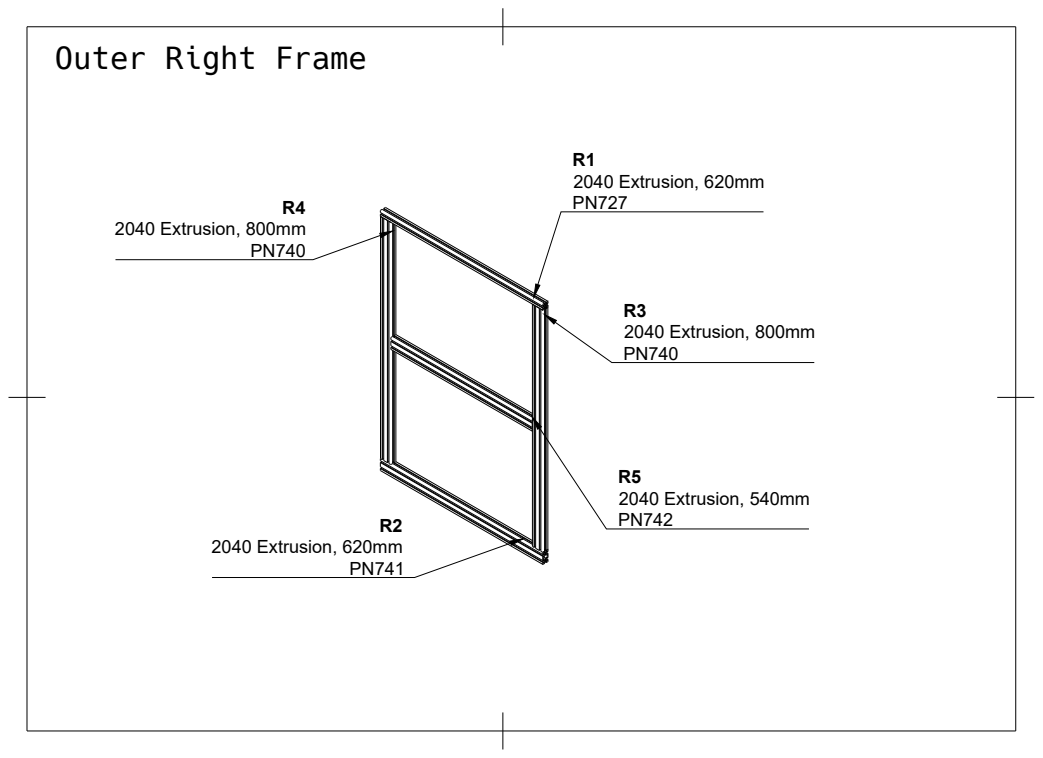
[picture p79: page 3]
2040 Extrusion, 620mm; 2040 Extrusion, 800mm; 2040 Extrusion, 540mm

Outer Right Frame

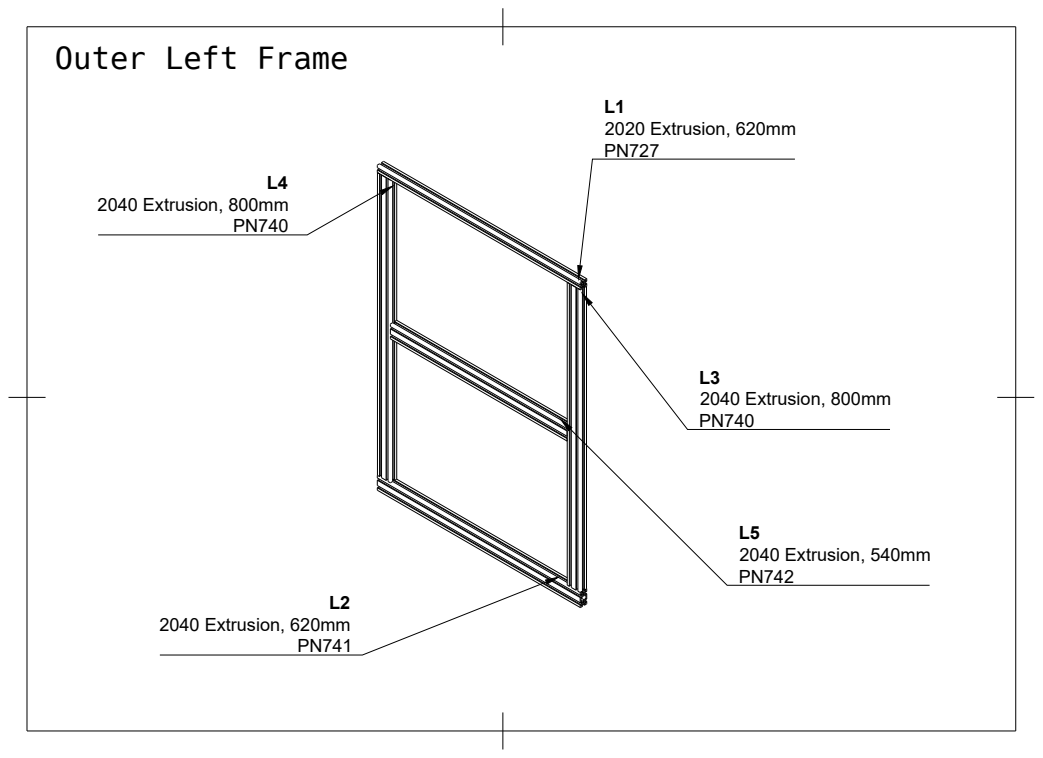
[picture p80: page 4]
2020 Extrusion, 620mm; 2040 Extrusion, 620mm; 2040 Extrusion, 800mm; 2040 Extrusion, 540mm

Outer Left Frame

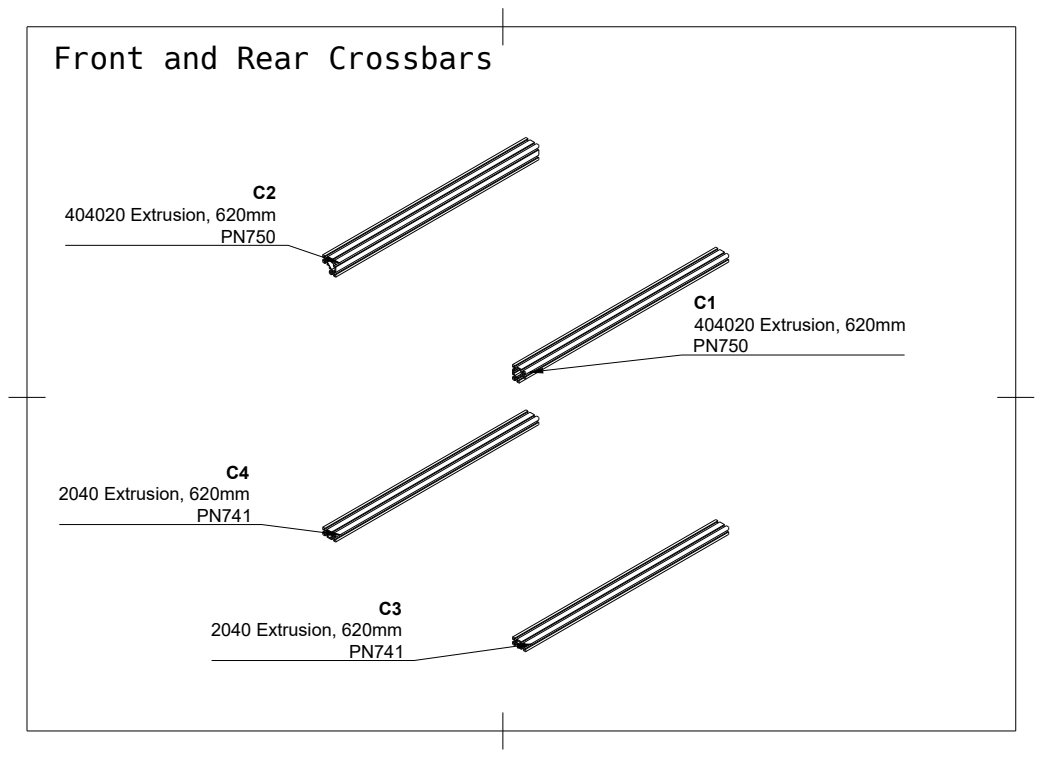
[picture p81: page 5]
404020 Extrusion, 620mm; 2040 Extrusion, 620mm

Front and Rear Crossbars

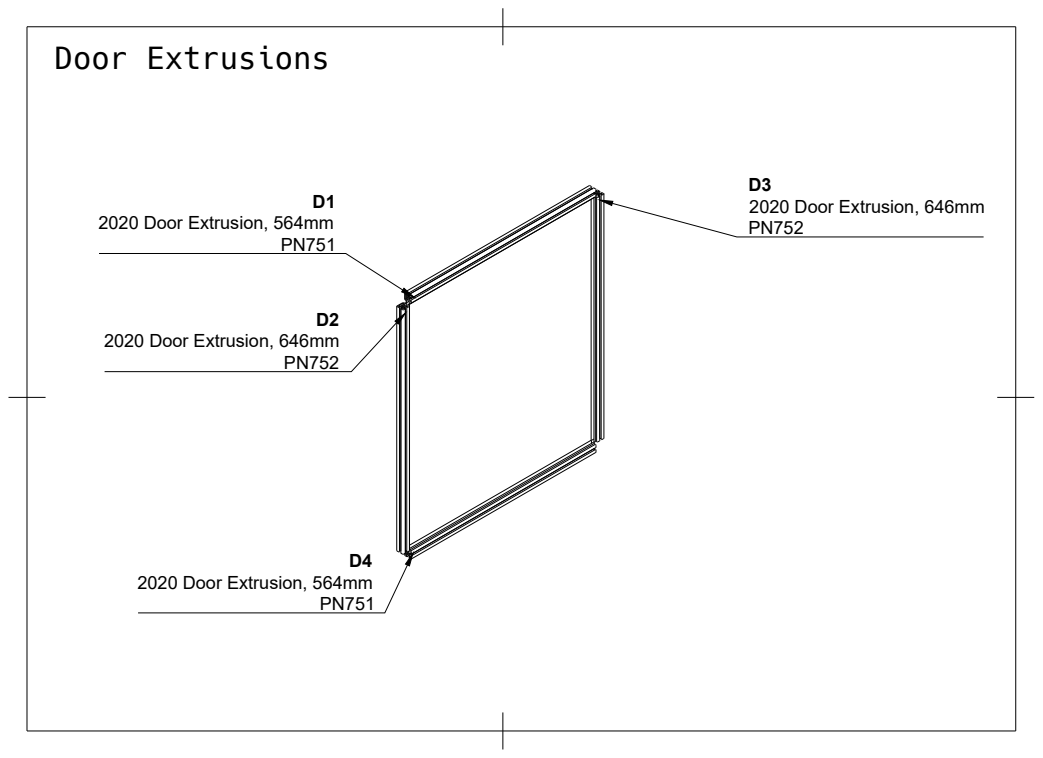
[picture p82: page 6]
Door Extrusions; 2020 Door Extrusion, 564mm; 2020 Door Extrusion, 646mm

2020 Extrusion, 540mm, Milled; 2020 Extrusion, 440mm, Milled; 2020 Extrusion, 620mm

XY Frame and X Crossbar

Bed Frame; 2020 Extrusion, 350mm; 2020 Extrusion, 220mm

Z Frame; 2020 Extrusion, 510mm; 2020 Extrusion, 540mm; 2020 Extrusion, 500mm

2020 Extrusion, 620mm

Electrical Mounting Bars

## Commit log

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2021-12-15 12/14 - Fixes, Bowden extruder, and a gantry lock
    - Fixed some issues with the left pulley component.
    - Fixed an incorrect peg hole depth on right mid `XY Joint`.
    - Added 5mm to the AB stepper mounts.
    - Pushed Y limit switch out ~20mm to allow clearance for the X limit switch. This is hacky, but will work and keep the bed area available.
    - Adjusted screw holes on right pulley component to account for the new limit switch mount.
    - Designed Bowden mount for BMG.
    - Designed `Gantry Lock` for servicing hotend and belts.
    - Raised the Y limit switch a bit to give clearance for heated inserts in the mount.
    [01 - XY - Pulleys - L Bottom.stl, 02 - XY - Pulleys - L Top.stl, 03 - XY - Pulleys - R Bottom.stl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]
2021-12-16 2021/12/15 - Mostly wiring
    - Tested XY motion
    - Designed and tested replacement for Z bottom bracket that includes rail alignment.
    - Tested all endstops
    - Added build plate
    - Sketched up panel mounts for JST-SM connectors for 2-6 pins and fit-tested
    - Began setting up wiring for JST-SM
    - Added STL Filename column to `Part Codes`
    - Crimped a lot of wires.
    - Created file for tracking wire codes and terminal names
    [19 - Z - Motion - Linear Rail Stop.stl, 19 - Z - Motion - Lower Rail Bracket.stl, Connectors.xlsx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]
2021-12-18 2021/12/17 Media and Wiring
    - Fixed issue with patch panels.
    - Terminated wires, probably terribly, but at least have the lengths and wrap done. Will re-crimp properly later (before using the wires).
    - Finished up the `T Slot Wire Anchor` design.
    - Tested panel mount--will need to be moved backwards.
    - Added a wire guide for the right `XY Joint` to keep the harness elevated.
    - Redesigned wire panel mounts to sit further back, leaving more room for exiting wire.
    - Added a folder for test GCODE and a basic movement test file, though it needs...testing.
    - Modified Z limit switches to lower them 6mm.
    - Discovered issue with BLTouch mount after attaching cable ties. Will probably try and move mou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
    [08 - XY - XY Joint - R Top.stl, 25 - Z - Motion - L Z1 Limit Switch.stl, 26 - Z - Motion - R Z2 Limit Switch.stl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]
2021-12-19 2021/12/18 - Fixes and board mounts
    - Fixed emboss on right patch panel
    - Revision 2 of XY Joint wire guide. Dealing with some elephant's foot.
    - Added a file for extending spare T slot underneath for mounting equipment. The file is parametric for the end-user's modification.
    - Designed clamps for board mounting
    - Added screw holes to board tray to secure it in place.
    - Modified blank tray template and exported STEP file to `/CAD` folder.
    - Rebuilt Octopus tray from template file.
    - Threw out the last four entries about clamps and boards and went with a simpler design with fewer parts and easier mounting.
    - Boards mount at an angle for easier access from the front.
    - Made parts for both Octo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
    [08 - XY - XY Joint - R Top.stl, 72 - Electrical - Wiring - R Panel Mount.stl, 76 - Electrical - Mount - L Octopus Board Mount.stl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]
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2021-12-20 12/20 - Fan mount, LED channel, and wiring stuff
    - Finished all crimps but ABL.
    - Started mapping headers and began Wiki with corresponding article.
    - Tested limit switches, fans, thermistors, bed heat, and finally first hotend heat and filament extrusion.
    - Designed mount for programmable LEDs. Design is parametric based on spacing, PCB width, and LED count. Includes a zip tie anchor.
    - LED tests. SP901E is finicky with WS2815, leaving it out for now.
    - Nearly all connectors are now labeled.
    - Resolved display issue.
    - Added a modification of an old PTFE tubing coupler design. This part should go away in later revisions.
    - First print should be tomorrow.
    [80 - Electrical - Fan Mount - 80mm Fan Mount.stl, 81 - Electrical - Fan Grill - 80mm Fan Grill.stl, 82 - Electrical - Lighting - LED Guide, WS2815.stl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]
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2021-12-22 12/22 - RPi Mount, Marlin Config
    - Preparing for vacation, so slowing activity.
    - Significantly cleaned up wiring in undercarriage area.
    - Added Marlin firmware modifications to source tree. Eventually switching to Klipper, but this is functional.
    - Slight modification to the SKR2 board mount to improve clearance beneath.
    - Created a Raspberry Pi board mount.
    [78 - Electrical - Mount - L SKR Board Mount.stl, 79 - Electrical - Mount - R SKR Board Mount.stl, 83 - Electrical - Mount - L RPi Board Mount.stl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]
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2021-12-27 12-26 - Frame caps
    - Significant work done on skirts:
    - Designed frame and section system. Front panels are modular and replaceable but fit together with screws.
    - Finished 92mm fan intake, right switch panel, two identical center grille pieces.
    - Work for screen and front communications ports can be done once back in office.
    - Rear panel has two grilles and two fan cutouts, plus an IEC panel mount spot.
    - Not entirely satisfied with fan cutouts, will work on them in the morning and push everything tomorrow.
    - Added #s 100-103, the caps to cover the exterior frame edges at the base and top.
    [100 - Exterior - Frame - Base Cap Type 1.stl, 101 - Exterior - Frame - Base Cap Type 2.stl, 102 - Exterior - Frame - Top Cap Type 1.stl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]
2021-12-27 12/27 - Undercarriage and skirts work
    - Finished rear exhaust and tagging pieces with IDs for the skirt.
    - Publishing 104-111 and reserving 112 and 113 for the display (to be done when back in office).
    - Fixed up the electronics undercarriage file with parts already designed.
    - Added PSU to the model and desgined a power supply mount, as well.
    [104 - Exterior - Skirt - L Front End.stl, 105 - Exterior - Skirt - R Front End.stl, 106 - Exterior - Skirt - L Rear End.stl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]
2021-12-28 12-28 - Numerous fixes
    - Fairly significant number of changes today.
    - Added a number of missing brackets in the model. I *believe* they are all present now, but will check WBIO (when back in office).
    - Fixed a few naming issues in the part codes list. Working on consistency and logical grouping. Re-numbering will come WBIO.
    - Iterating through the models and making sure all fasteners are present.
    - Added a TPU vibration damper between the AB stepper mounts and the frame. I will test TPU washers WBIO.
    - Fixed minor issues with tensioner assembly/disassembly.
    - Inset M3s on the tensioner top and added chamfers for screw head insertion/removal.
    - Removed #97 after integrating wire guide into t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
    [08 - XY - XY Joint - R Top.stl, 11 - XY - Tensioner - Bolt Receiver.stl, 12 - XY - Tensioner - Idler Seat.stl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]
2021-12-30 12/29 & 12/30 - Many fixes; see changelog
    ## 2021-12-30
    - Added some bracing to the electrical panel mounts to reduce flex and moved them further back.
    - Introduced the wiring panels to the master model.
    - Added lighting into the model for 3 x 12 pixel strips at 60px/m (16.6mm spacing).
    - Made a few fixes to the lighting strip so the zip tie does not cross over an LED.
    - Plenty of new renders.
    ## 2021-12-29
    - Fixed ABL mount issues with belt attachment screws.
    - Also simplified mounting the hotend fan. Two screws mount into the fan shroud and two pass through to mount both. The fan shroud and fan then can come off with two screws instead of four.
    - Added motion joints.
    - Reviewed assembli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
    [13 - XY - Tensioner - Tensioner Cap.stl, 30 - X Gantry - Carriage Mount.stl, 31 - X Gantry - Top Mount.stl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]
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2022-01-02 01/01 - 01/02 - Minor fixes
    ## 2022-01-02
    - Tweaked frame caps so the screw holes are more printable
    - Re-exported X gantry's front plate.
    ## 2022-01-01
    - Back in office. 31 parts to print until I'm caught up.
    - Strengthened PSU bracket
    - Switched to M4 screws for PSU bracket (oops)
    - Modified fan exhaust and intakes to print properly. Fan mount had impossible overhangs; this is fixed.
    - Tweaked tolerance for IEC plug
    [100 - Exterior - Frame - Base Cap Type 1.stl, 101 - Exterior - Frame - Base Cap Type 2.stl, 102 - Exterior - Frame - Top Cap Type 1.stl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]
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2022-01-06 01/06 - Panel mount tweaks
    - Shortened tops of wiring panel mounts to leave space for flooring panel to inset.
    [72 - Electrical - Wiring - R Panel Mount.stl, 73 - Electrical - Wiring - L Panel Mount.stl]
2022-01-08 01/07 - Left wire panel rework
    - Printing was delayed by layer shifting on the 92mm fan mount.
    - Did a relayout on the left panel mount. The Fusion timeline is more manageable and the layout of the connectors more logical.
    - Front panel mounts all fit save for Ethernet and SD Card--expect those to arrive today.
    - Added zip tie anchors to the forward-facing side of the panel mount.
    - RJ-45 cutout is off by a bit, but it fit after some effort. Going on the TODO list.
    [113 - Exterior - Skirt - Display Slot.stl, 71 - Electrical - Wiring - L Panel Plate.stl, 72 - Electrical - Wiring - R Panel Mount.stl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]
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2022-01-10 Hotend mounting simplification
    - Hotend now locks in place with two screws into the mount itself, rather than passing through to the front plate. This allows preassembly of the hotend and fewer screws to remove the mount plate for belt access (4->2).
    - Between the above and changing the fan screws, the hotend cage, fan and all, can be removed with 4 total screws instead of 8.
    - Fixed an issue with the front mount plate's vent not passing all the way through.
    - Steadily adding 0.4mm chamfers to narrow holes (mostly screw holes) that touch the build surface in case of elephant's foot. Completed hotend and stepper mount modification so far.
    - Also moving ID # off the build surface if an alterna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
    [16 - XY - Steppers - Stepper Mount.stl, 30 - X Gantry - Carriage Mount.stl, 32 - X Gantry - Back Plate.stl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]
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2022-01-12 Camera, stepper mount, FAQ skeleton
    - Fixed mounting hole size for part cooling fan.
    - Created a skeleton FAQ.
    - Added a note in the `/Firmware/Klipper` folder where to find the `.cfg` files for Klipper.
    - Testing virgin coconut shell activated carbon for oxidation. Hopefully this is a good supplier.
    - Raised A/B steppers a few mm. Now use M5x45mm screws.
    - Lots of issues resolved on the X Gantry and hotend.
    - Changed mointing direction for part cooling fan. Heated insert no longer enters at an angle, which should help alignment issues.
    - BLTouch mount works.
    - Pretty much every component touched to update `Parameters` file. No changes due to new parameters yet.
    - Went through a number of it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
    [16 - XY - Steppers - Stepper Mount.stl, 32 - X Gantry - Back Plate.stl, 33 - X Gantry - Front Plate.stl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]
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2022-01-15 XY Joint and XY Pulleys polish, FAQ update
    ## 2022-01-15
    - Activated carbon appears to be a good supplier. No sign of rust on any of the test items.
    - Updated the FAQ a bit.
    ## 2022-01-14
    - Waiting on HEPA filters so working on polishing XY components for milestone print.
    - Added surface chamfers to XY Pulleys, XY Joint components.
    - Fixed #1 and #2 ID text to specify that they are Left side components.
    - Redid #8, R Top XY Joint. Center rib now stretches to the wire anchor, the anchor is slightly deeper, and there is now a lip around the rear edge.
    - Found a screw hole that somehow got lost on #10.
    [01 - XY - Pulleys - L Bottom.stl, 02 - XY - Pulleys - L Top.stl, 03 - XY - Pulleys - R Bottom.stl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]
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2022-01-20 Lots of filtration work
    ## 2022-01-20
    - Will need TPU shims to leave room for tubing connectors.
    - Fixed fan holes to fit regardless of orientation.
    - Added foot to 75mm fan intake.
    - Added small front foot to use with 75mm fan intake
    - Modeled 75mm radial fan
    ## 2022-01-19
    - Dual 50mm seem like they would work for a small chamber, particularly with one 50mm running continuously as exhaust.
    - Modeled and started a FPD for dual 75mm blowers.
    - Looking into flexible hosing, ordered 1/4" ID, 1/2" OD silicone tubing and push connectors.
    - Dual 75mm is front-heavy.
    [50mm Fan Exhaust.stl, 75mm Fan Exhaust.stl, AC Duct.stl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]
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2022-01-21 Pushing current filtration work
    - Made shims/TPU gaskets for both 75mm and 50mm fans. They push the fans out 1.6mm to make room for a hose adapter (and dampen noise).
    - Both the 50mm and 75mm fan intakes work, though the right 50mm profile is incorrect.
    - Working on 75mm fan exhaust to tighten fit. Modeling is difficult as there is some variation between brands in wall thicknesses, etc.
    - Ordered 1" ID hose instead of 1/4". The 75mm fan is having difficulty providing pressure, so I'm going to try avoiding necking down. The 1/4" hosing may still be useful for 50mm fans.
    - 1/4" hose is ideal for 50mm fan.
    - 50mm fan intake is now front heavy with hose on, added hole for an insert and foot.
    - S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
    [50mm Fan Exhaust Adapter (TPU).stl, 50mm Fan Exhaust.stl, 50mm Fan Intake Gasket (TPU).stl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]
2022-01-22 Editing and cleanup
    - Removed Marlin firmware folder. It's not maintained or even finished, nor do I intend to move away from Klipper now.
    - Reworded some of the readme.md and slimmed it down. Moved the TODO entirely to Issues.
    - Moved orientation-specific STLs for filtration to subfolders.
    - Added a small hole to the center of the 75mm tank to add more perimeters for sturdiness. The center pillar is pretty weak.
    - AC -> HEPA duct is done for the vertical filtration assembly.
    [50mm Fan Intake.stl, 75mm Fan Intake.stl, AC Tank - 75mm.stl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]
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2022-02-10 Stale STL cleanup, BOM prep
    ## 2022-02-09
    - Moving through components to add part numbers and locate model inconsistencies.
    - Resolved some very old model components that didn't get updated against the prototype.
    - `Printer Pard Codes.xlsx` has a significant update with tabs for each BOM category.
    - Fusion model now is largely updated with internal part codes for auto-generating a BOM.
    - Python script for scraping part numbers and instances is initially done.
    - Removed a lot of unused and outdated files from the Fusion project.
    - Removed PN080 and PN081, the freestanding 80mm fan mount and grille, along with some other stale entries.
    - Exported XY Pulleys and XY Joints again for final repri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
    [01 - XY - Pulleys - L Bottom.stl, 02 - XY - Pulleys - L Top.stl, 03 - XY - Pulleys - R Bottom.stl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]
2022-02-10 BOM progress
    - Continuing fresh reprints. May have discovered an issue with the tensioner.
    - Adding reference links to the BOM.
    - Most parts are now in the BOM--looking to address issues like zip ties and other oddments
    - Considering using placeholder (empty) bodies with part numbers to trigger the script when scraping for BOM.
    [11 - XY - Tensioner - Bolt Receiver.stl, 12 - XY - Tensioner - Idler Seat.stl, 13 - XY - Tensioner - Tensioner Cap.stl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]
2022-02-12 Updated part codes, pushed part number script
    ## 2022-02-11
    - Tensioner definitely needs rework.
    - Removed PN100-PN103, the frame caps. With wood paneling, they are unnecessary.
    - Pushing the `ExtractBOM_PN` Fusion script.
    - Re-exporting files and continuing reprints before disassembly.
    - Added a lot of entries that are not modeled, like heat shrink and zip ties.
    - Most entries in the parts list now have links to reference suppliers
    - New 80mm fan mounts for front and rear panels, with PNs 102 and 103
    [100 - Exterior - Frame - Base Cap Type 1.stl, 101 - Exterior - Frame - Base Cap Type 2.stl, 102 - Exterior - Frame - Top Cap Type 1.stl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]
2022-02-12 Parametric tools, 80mm fans, and near-final part codes
    - Exported parametric tools for heated inserts.
    - Changed a few part categories and added a "Type" column for parts.
    - Modified the 80mm fan grill for better printing.
    - I believe all but some very odds-and-ends parts have numbers, so closing issue #20.
    [103 - Exterior - Skirt - 80mm Fan Grille.stl, M3 Heat Set Insert Practice Block.f3d, M3 Heat Set Insert Practice Block.stl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]
2022-02-13 Moved Part Codes to /BOM, fixed #1
    - Temporarily removed the part codes Markdown file, as it is not current. Too many changes are taking place with the BOM to keep up.
    - Renamed `Printer Part Codes.xlsx` to `Part Codes.xlsx` and shifted it to the `/BOM` folder.
    - Replaced stock nuts with anti-backlash in the model, fixed some missing screws in the `Z Master`
    - Adjusted RPi panel mount connector profiles. The skirt is now fully modeled and should be correct in the BOM. Also tested and working.
    [104 - Exterior - Skirt - L Front End.stl, Part Codes.xlsx, Printer Part Codes.xlsx]
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2022-02-16 BOM and model updates
    ## 2022-02-15
    - Fixed a ton of minor issues with brackets in the model.
    - All brackets are now properly positioned and should be propogated.
    - Removed brackets from the bed frame; will rely solely on printed parts.
    - Bracket assemblies still used SHCS instead of button head; fixed and propagated.
    - Filtration is in the model.
    - Finished renaming printed part numbers.
    - SP901E has a placeholder body with fasteners in the model, temporarily addressing #21 .
    ## 2022-02-14
    - Fixed outer frame for part ID purposes.
    - Added invisible SP901E assembly to the model to get it and the appropriate fasteners inventoried.
    - Updated base foot and LED strips for part numbers.
    - Too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
    [200 - Filtration - Fans - Exhaust Adapter (TPU).stl, Connectors.xlsx, Part Codes.xlsx]
2022-02-17 Fixed RPi, worked on BOM
    - Raspberry Pi board mounts (PN083, PN084) are now horizontal to allow better airflow.
    - Part numbers are now broken out into "General Part List" and "Printed Part List"
    - All part numbers are now three digit.
    - Created wire anchor assembly.
    - Door frame assembly is modeled, minus the hinges.
    - Concerned hinge gap is too small for door frame, or may leave too large a gap on the handle side. May need to design printable hinges to properly align.
    [83 - Electrical - Mount - L RPi Board Mount.stl, 84 - Electrical - Mount - R RPi Board Mount.stl, General Part List.xlsx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]
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2022-02-18 Fixed tensioner cap
    - Updated `Connectors.xlsx` to reflect minor changes.
    - PN013, Tensioner Cap: fixed issue with impossible to print features. M5x25 instead of M5x16 screws are needed. They're already needed for the tensioner bolt iself, so no new fasteners are introduced.
    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
    [13 - XY - Tensioner - Tensioner Cap.stl, Connectors.xlsx]
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2022-02-21 PTFE guide is ready
    ## 2022-02-21
    - PN100 is finished. PTFE tube stays neatly out of the way and has a shorter feed path.
    - Adding new milestones and issues to help sort short- and long-term goals.
    ## 2022-02-20
    - Iterating through PN100 to get a satisfactory design.
    - Nearly all internal connector wires have a prespecified length now. I will leave the undercarriage unspecified as it's short enough it can be left to the end user. Plus no two people are going to want to arrange it the same way.
    - Not a lot of model progress today; focused on wiring.
    - Now using a PTFE tube to stiffen the hotend wiring loom. No filament is in it--it just adds rigidity.
    [100 - XY - Wiring - Rear PTFE Tube Guide.stl]
2022-02-22 Parts, connectors, and minor fixes
    ## 2022-02-22
    - Adjusted PN083/PN084 clearances around the extrusion.
    - Tweaking master part list entries a bit, adding "Supplies" category that includes items of indeterminate quantity (e.g. lubricant) or that may be on hand as a tool (e.g. screwdrivers) and generally don't go on a BOM but will be needed.
    - Removed old PN082 file.
    - Rebalanced screws on the Z Gantries. There are now three M5 on top, three under.
    - Finished insulation and fasteners for all of the panels but the flooring.
    - Updated the master model and removed old paneling.
    - Added in feet to the `Outer Frame` model.
    - Turns out PN083 and PN084's issues are not thickness und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
    [21 - Z - Motion - L Gantry.stl, 22 - Z - Motion - R Gantry.stl, 27 - Z - Motion - L Lead Screw Plate.stl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]
2022-02-23 Stepper mount work
    ## 2022-02-23
    - Modified AB stepper mounts and TPU shim to sit on top panel.
    - Extended AB stepper mount height, now uses M5 x 60mm BHCS.
    - Added PN089, a stepper alignment slider. It's a TPU plug for where the linear rods from the AB steppers enter the top panel. A ball bearing sits in it and plugs the bottom to keep it airtight, but the top has room for the bearing to slide sideways to get it precisely positioned.
    - Added some lateral clearance for the stepper mounting holes, as well.
    - Removed `AB Stepper Modules` from the `XY Master` and pulled it into the `Master` file because it mounts above the enclosure.
    - BOM tweaks.
    [15 - XY - Steppers - Vibration Damper (TPU).stl, 16 - XY - Steppers - Stepper Mount.stl, 89 - XY - Motion - Stepper Alignment Slider.stl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]
2022-02-25 New couplers, lots of part list fixes
    ## 2022-02-25
    - Lots of part corrections in the model.
    - Modeled and added the 3mm spring steel build plate.
    - Finished the front door and related components in the model. Added M5x14 FHCS to the BOM.
    - Cleaned up the frame components to be external references instead of internal. Will fix the XY and rest of Z axis tomorrow.
    - PTFE coupler and hose exhaust work well--will need TPU guide between the pneumatic couplers to align the PTFE tubes.
    ## 2022-02-24
    - Assembled and measured door. Approximate clearance with MISUMI hinges is 4-5mm on the handle side.
    - FPD of hose exhaust and PTFE coupler for side panels. Adding PN120 and PN121.
    - Testing stabilit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
    [120 - Exterior - Frame - Exterior PTFE Coupler.stl, 121 - Exterior - Frame - Exhaust Hose Coupler.stl, 90 - Misc - Frame - Corner Bracket Cover.stl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]
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2022-02-28 FIxes to side panel couplers
    - Added PN122, a PTFE tube guide for between the pneumatic connectors for PN120
    - Fixed outside panel coupler dimensions for new panel widths.
    - Moved some brackets slightly to work with thicker floor panel.
    - Modeled all remaining insulation and added relevant parts.
    - Finished adding fasteners to the floor panels.
    - Working on ensuring the air filtration both fits and can exhaust easily. This may require work, but is doable.
    [120 - Exterior - Frame - Exterior PTFE Coupler.stl, 121 - Exterior - Frame - Exhaust Hose Coupler.stl, 122 - Exterior - Frame - PTFE Coupling Guide (TPU).stl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]
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2022-03-01 Part list updates & fixes and a few new renders
    ## 2022-03-01
    - Moved exhaust hose and PTFE coupler exits. Panels are no longer identical but this is much simpler to work around.
    - FPD of wire conduit for the paneling. Since there is no physical paneling yet, the conduit will definitely need revision later. This is mostly to ensure it's doable, counted in the BOM, and have *something* to test when the paneling is fabricated.
    - Model is now missing only lock collars for the F688 alignment bearings.
    - Only remaining design necessary for a complete prototype are TPU gaskets for the front door. Changes definitely need to be made around the hotend and (later) the Z axis, but an enclosed prototyp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
    [General Part List.xlsx, Printed Part List.xlsx, test_bom.xlsx]
2022-03-02 BOM progress
    ## 2022-03-02
    - Began verification of BOM and model.
    - Replaced M5x12 SHCS for the doors with M5x16.
    - Shortened air filter base stand top 2mm.
    [207 - Filtration - Misc - Base Stand.stl, General Part List.xlsx, test_bom.xlsx]
2022-03-03 BOM verification
    ## 2022-03-03
    - Continued model/BOM verification.
    - Lots of fastener adjustments, but no major surprises
    - The electrical panel mount will definitely need redesign, and the PSU mount is dubious.
    - Also need a mount for the new RPi buck converter.
    [General Part List.xlsx, test_bom.xlsx]
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
